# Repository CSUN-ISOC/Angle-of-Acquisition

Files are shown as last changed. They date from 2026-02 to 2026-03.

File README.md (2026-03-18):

# Angle-of-Acquisition
This is the repository for the AoA (Angle of Arrival) team's work throughout the semester. All files (source code and design files) relating to the AoA team and the Fibonacci Sphere can be found in this repository. Branches of this repository are meant for team members of the AoA team and their individual contributions to the project.

The primary goal of the AoA team this semester is to improve the design of the sphere and to give it the ability to adjust its positioning depending on the angle of an incoming modulated signal from a laser diode.

# Simulations


### Figure 1

Figure 1 shows the design of the 3D-printed servo mount in CAD. This servo will allow the sphere to rotate 360 degrees and tilt 15 degrees in each direction.



### Figure 2

Figure 2 shows a MATLAB simulation confirming proper operation of the entire Angle of Acquisition system. In this simulation, a theoretical flashlight is shined at the Fibonacci Sphere. The Fibonacci Sphere can identify where on the sphere the beam of light is shining by using data from all 64 of the photoresistors mounted on the sphere. From this, the sphere positions itself to make the beam of light shine on a receiver mounted to the exterior surface of the Fibonacci Sphere and thus allow the receiver to "focus" on the incoming data encoded into light source. The position of the flashlight changes every four seconds, and within those four seconds, the sphere is expected to move accordingly to line up the receiver to the beam of light. The square waves show the different positions of the light and the decaying graphs show the initial large error, which approaches zero in less than one second, meaning that the sphere properly identified the position of the incoming light and positioned the receiver as intended. This quick adjustment however, raised concerns about the forces that would result on the sphere, so the repositioning speed of the sphere was adjusted to be much slower. Even considering this adjustment, the sphere still has enough time to position itself and receive all of the incoming data.



### Figure 3

Figure 3 shows the design file for one quarter of the sphere. Due to its size, the Fibonacci Sphere had to be printed in quarters and attached together after the fact.

# Video Demonstrations
- Rotating the Fibonacci Sphere using Dummy Code:
  
  ISOC_Project

# Testing Documentation
The following media displays the testing that has gone into the designing, building, and programming of the Fibonacci Sphere and its respective circuitry.



### Figure 1

Figure 1 shows the initial attatchment of the servo mount that supports the sphere and is meant to allow the sphere to both rotate and tilt.



### Figure 2

Figure 2 shows how the servo mount is internally attached to the Fibonacci Sphere via nuts and bolts. Thread locker has been added to avoid loosening under vibration and/or shock.



### Figure 3

It was soon realized that the original shielded wiring that was used (black wires shown in Fig.2) were not necessary and were only more difficult to work with (i.e. to solder) due to them being frayed wires rather than solid. Figure 3 shows the old wires switched out for new red/blue wires with a solid core that allowed for easier soldering and a lighter load on the servo and its mount.



### Figure 4

Figure 4 gives a closer look at the wires inside the sphere to show that all wires have been labelled so that they can be connected to their proper terminals. Red wires all need to go to V<sub>CC</sub> and the blue wires will later be labeled to indicate which channel on which of the four multiplexers they belong to. This is to make diagnosis easier in the future.

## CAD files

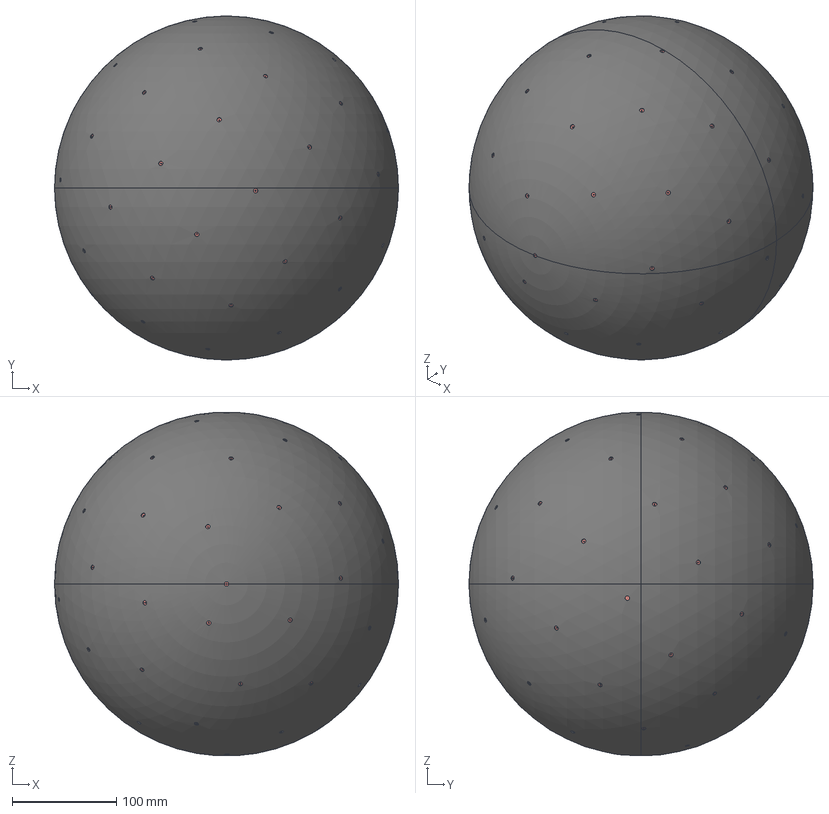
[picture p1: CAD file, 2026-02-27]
Sphere Design Files/Copy of Fibonacci Sphere v4 Whole.step
330.2 x 330.2 x 329.6 mm

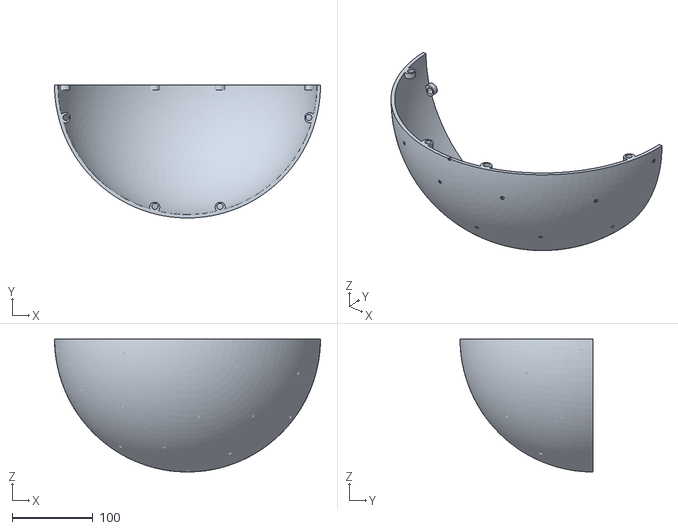
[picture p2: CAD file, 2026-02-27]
Sphere Design Files/Copy of Fibonacci Sphere v3 Bottom RIght.stl
330.2 x 165.1 x 165.0

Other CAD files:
Sphere Design Files/Copy of Fibonacci Sphere v4 Bottom Left.stl
Sphere Design Files/Copy of Fibonacci Sphere v4 Top Left.stl
Sphere Design Files/Copy of Fibonacci Sphere v4 Top RIght.stl
Sphere Design Files/Copy of Fibonacci Sphere v3 Whole.step

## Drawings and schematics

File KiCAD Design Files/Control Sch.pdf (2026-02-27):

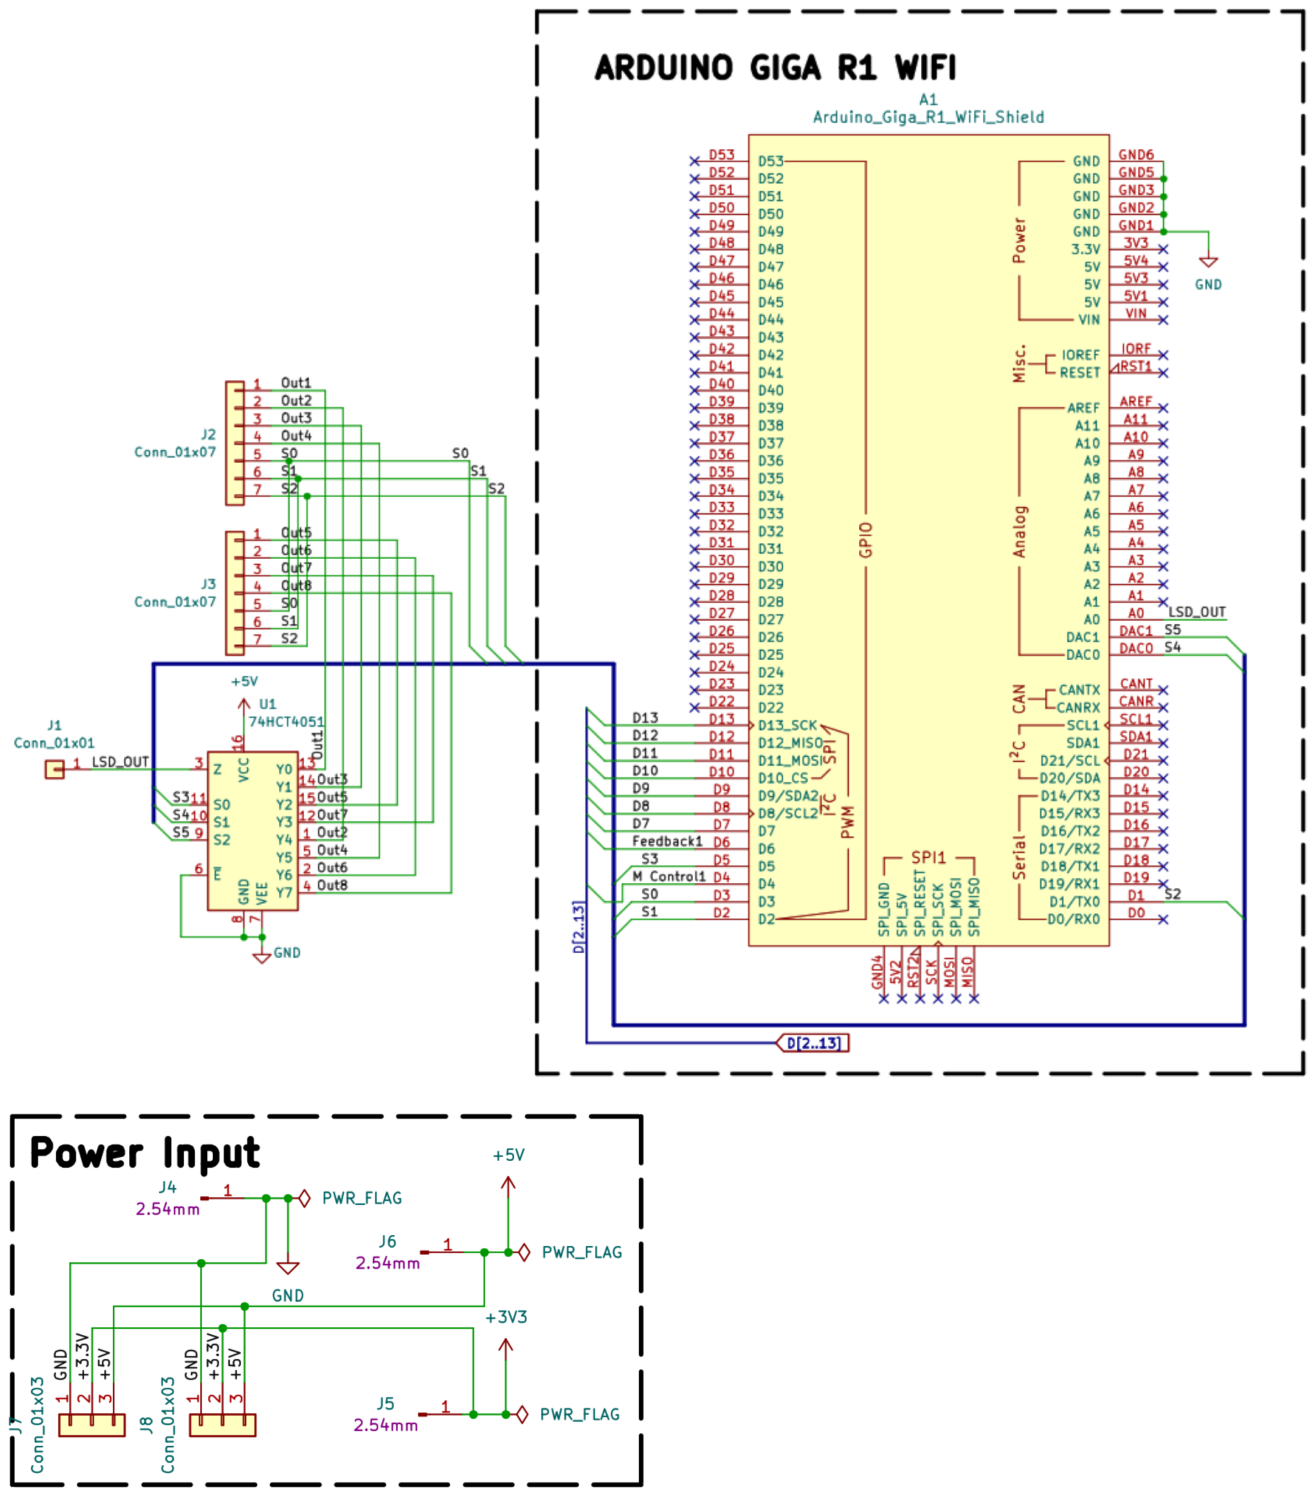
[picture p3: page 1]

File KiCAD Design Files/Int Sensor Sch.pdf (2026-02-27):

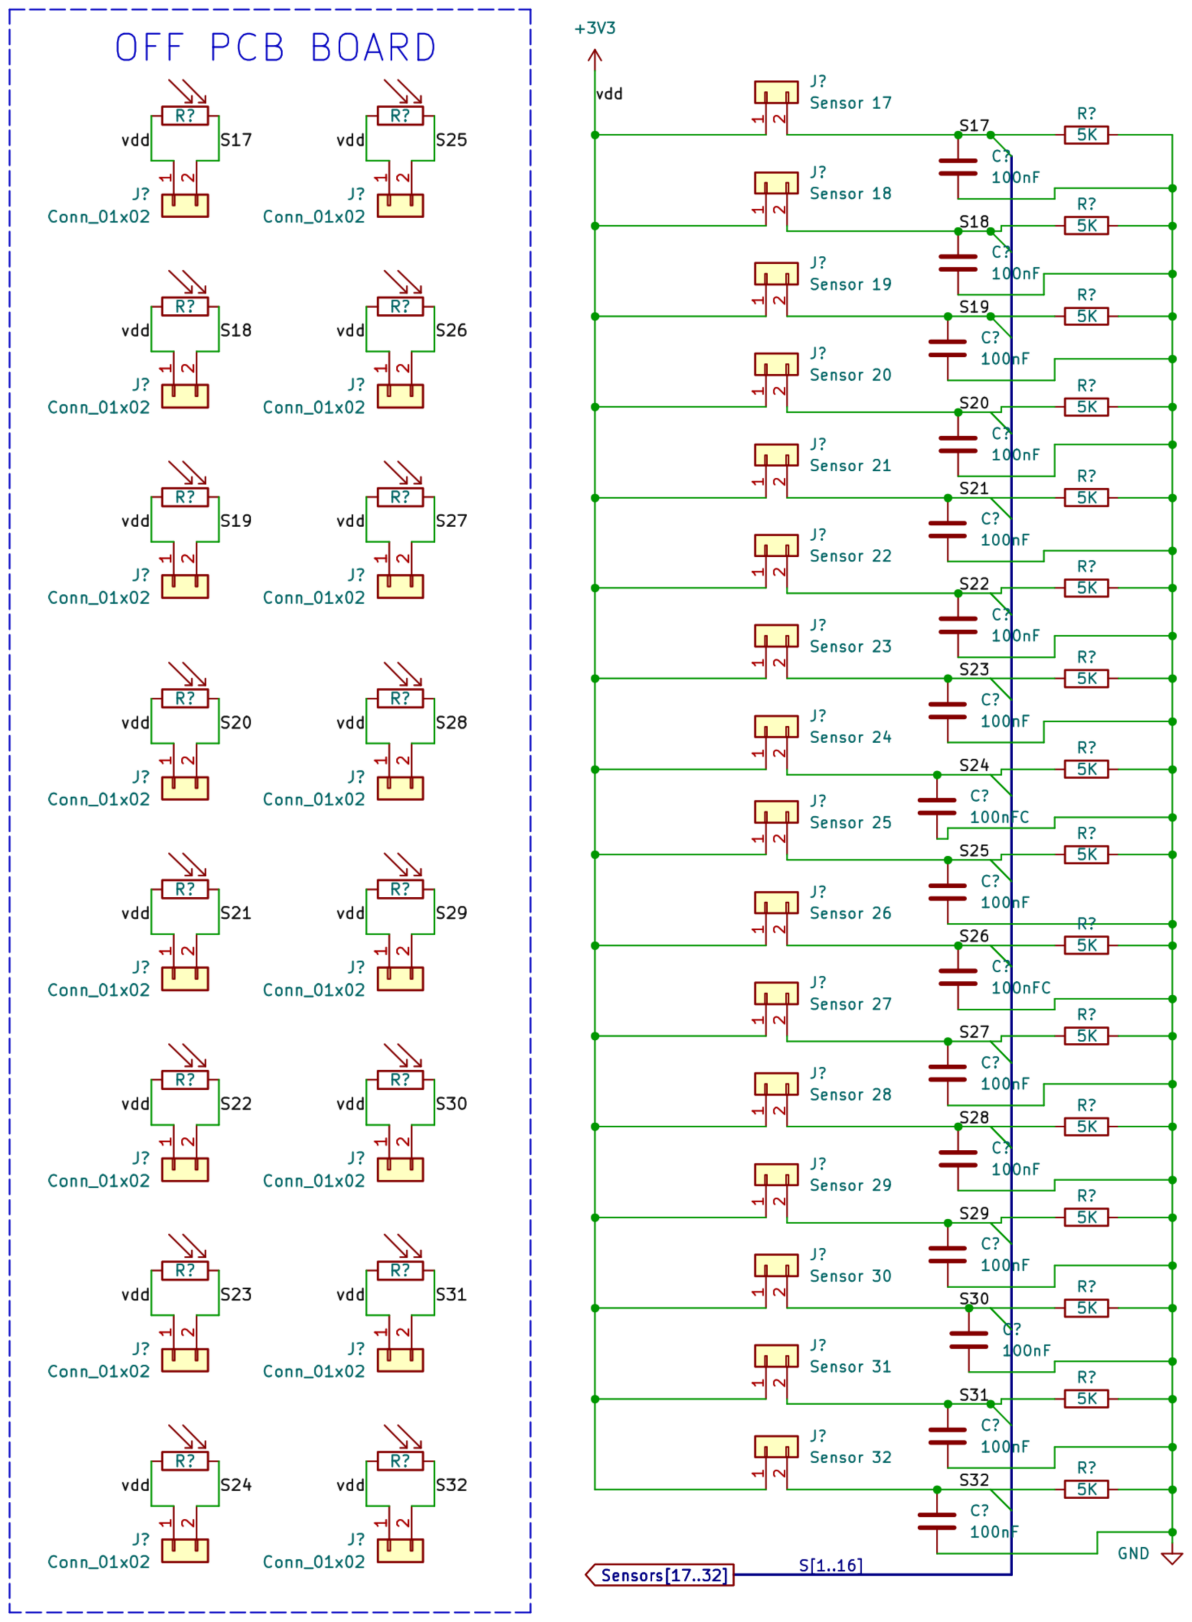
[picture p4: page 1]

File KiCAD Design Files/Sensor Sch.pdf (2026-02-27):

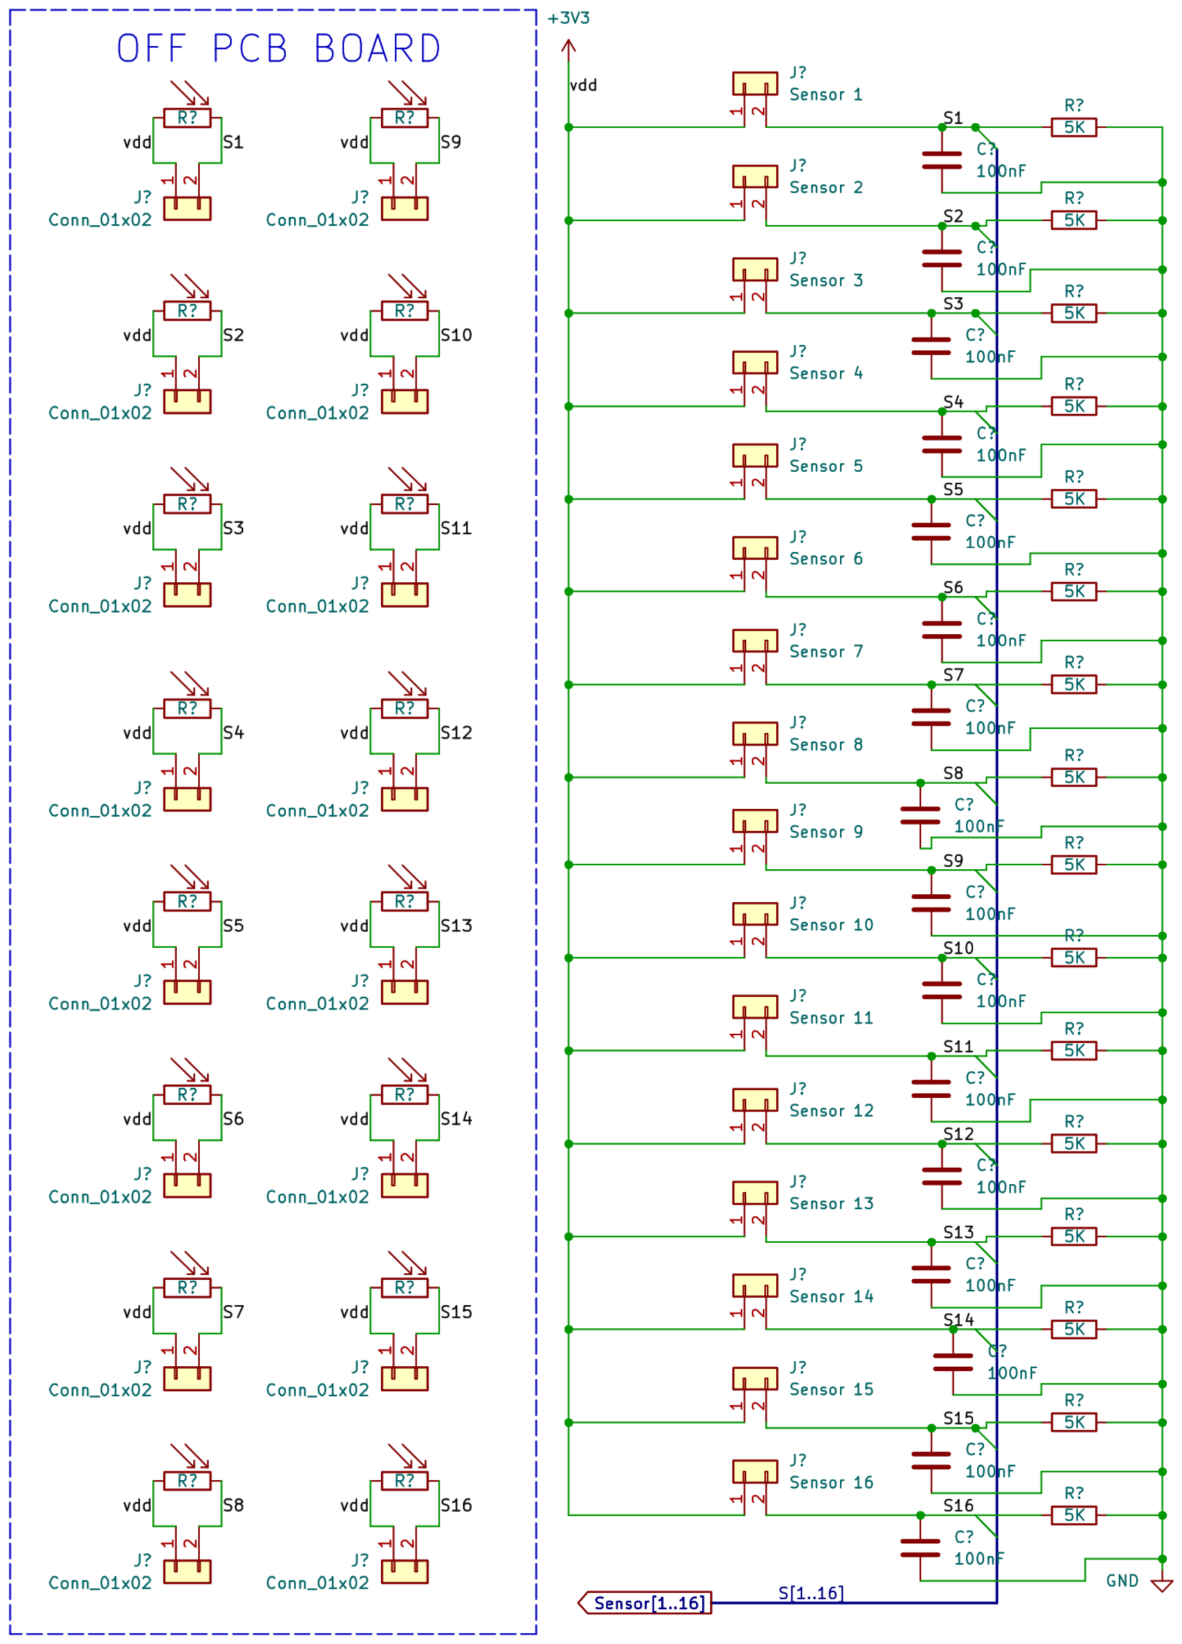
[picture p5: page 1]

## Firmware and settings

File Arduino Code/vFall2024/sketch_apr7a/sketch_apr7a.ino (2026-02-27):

#include "globals.h"
#include "matrix.h"
#include "muxControl.h"
#include "lightArray.h"
#include "FeedBackServo.h"
#include <RPC.h>

// Define pins
#define FEEDBACK_PIN 6   // Feedback pin connected to the feedback signal from the servo
#define SERVO_PIN 4      // Control pin for the servo

uint32_t activeSensor;
float* testIntensityReadings;

// set feedback signal pin number and constants
FeedBackServo feedbackServo(FEEDBACK_PIN);  // Create a FeedBackServo object

void setup() {
  /*
  // put your setup code here, to run once:
  //check to see which core is current
  pinMode(LEDB, OUTPUT); //blue led for M7
  pinMode(LEDG, OUTPUT); //green led for M4
   if(RPC.cpu_id() == CM7_CPUID){
    blink(LEDB, 100); //blink  blue led (M7 Core)
   } else {
    blink(LEDG, 100); //blink green led(M4 core)
   }
  RPC.begin(); //initialize 2nd core
  //end of core check
  */

  pinMode(LED_BUILTIN, OUTPUT);
	activeSensor= 0; //currently selected sensor
	testIntensityReadings = nullptr; //initialize test intensity readings
	lightArrayInit(activeSensor); //initialize mux controls
  Serial.begin(9600);
  analogReadResolution(12);
  pinMode(D5, OUTPUT);
  pinMode(D3, OUTPUT);
  pinMode(D2, OUTPUT);
  pinMode(D1, OUTPUT);
  lightArrayBaseline(); //take baseline
  
  digitalWrite(LED_BUILTIN, LOW);   // turn the LED off by making the voltage LOW
  digitalWrite(LED_BUILTIN, HIGH);  // turn the LED on (HIGH is the voltage level)
  delay(100);                      // wait for a second
  digitalWrite(LED_BUILTIN, LOW);   // turn the LED off by making the voltage LOW
  delay(100);                      // wait for a second
  digitalWrite(LED_BUILTIN, HIGH);  // turn the LED on (HIGH is the voltage level)
  delay(100);                      // wait for a second
  digitalWrite(LED_BUILTIN, LOW);   // turn the LED off by making the voltage LOW
  delay(100);                      // wait for a second
  digitalWrite(LED_BUILTIN, HIGH);  // turn the LED on (HIGH is the voltage level)
  delay(100);                      // wait for a second
  digitalWrite(LED_BUILTIN, LOW);   // turn the LED off by making the voltage LOW
  delay(100);                      // wait for a second
  digitalWrite(LED_BUILTIN, HIGH);  // turn the LED on (HIGH is the voltage level)
  delay(100);                      // wait for a second
  digitalWrite(LED_BUILTIN, LOW);   // turn the LED off by making the voltage LOW
  

  //servo part, sets motor pin
  feedbackServo.setServoControl(SERVO_PIN);  // Attach the servo control to the pin
  feedbackServo.setKp(1.0);  // Optional: Set a custom proportional gain for rotation
}

void loop() {
  lightArraySampleSensors();

  for (int i = 0; i < g_sensorCount; i++) {
    Serial.print("Sensor[");
    Serial.print(i);
    Serial.print("]: ");
    Serial.print(100 * g_sensorIntensityVector.element[i][0], 5);
    Serial.print("% - ");
    Serial.println(g_muxADCReadings[i]);
  }

  auto [azimuth, elevation] = lightArrayCalculateAoA3D();

  Serial.print("Azimuth: ");
  Serial.print(azimuth, 2);
  Serial.print("°, Elevation: ");
  Serial.print(elevation, 2);
  Serial.println("°");
  delay(500);

  // Rotate to Azimuth
  Serial.print("Rotating to AoA Azimuth: ");
  Serial.println(static_cast<int>(azimuth));
  feedbackServo.rotate(static_cast<int>(azimuth), 4);

  delay(1000);  // Wait 1s between readings
}

  /*
  //leds that turn on trying to show that it is being setup
  digitalWrite(LED_BUILTIN, HIGH);  // turn the LED on (HIGH is the voltage level)
  delay(200);                      // wait for a second
  digitalWrite(LED_BUILTIN, LOW);   // turn the LED off by making the voltage LOW
  delay(200);                      // wait for a second
  digitalWrite(LED_BUILTIN, HIGH);  // turn the LED on (HIGH is the voltage level)
  delay(200);                      // wait for a second
  digitalWrite(LED_BUILTIN, LOW);   // turn the LED off by making the voltage LOW
  */

  // Serial.println("Sensor[1]: ");
  // Serial.println(testIntensityReadings[1],32);
  // Serial.println("Sensor[2]: ");
  // Serial.println(testIntensityReadings[2],32);
  // Serial.println("Sensor[3]: ");
  // Serial.println(testIntensityReadings[3],32);
  // Serial.println("Sensor[4]: ");
  // Serial.println(testIntensityReadings[4],32);
  // Serial.println("Sensor[5]: ");
  // Serial.println(testIntensityReadings[5],32);
  // Serial.println("Sensor[6]: ");
  // Serial.println(testIntensityReadings[6],32);
  // Serial.println("Sensor[7]: ");
  // Serial.println(testIntensityReadings[7],32);
  // Serial.println("Sensor[8]: ");
  // Serial.println(testIntensityReadings[8],32);
  // Serial.println("Sensor[9]: ");
  // Serial.println(testIntensityReadings[9],32);
  // Serial.println("Sensor[10]: ");
  // Serial.println(testIntensityReadings[10],32);
  // Serial.println("Sensor[11]: ");
  // Serial.println(testIntensityReadings[11],32);
  // Serial.println("Sensor[12]: ");
  // Serial.println(testIntensityReadings[12],32);
  // Serial.println("Sensor[13]: ");
  // Serial.println(testIntensityReadings[13],32);
  // Serial.println("Sensor[14]: ");
  // Serial.println(testIntensityReadings[14],32);
  // Serial.println("Sensor[15]: ");
  // Serial.println(testIntensityReadings[15],32);
  



/*
//code core check
void blink(int led, int delaySeconds) {
    for(int i; i < 3; i++) {
      digitalWrite(led, LOW);
      delay(delaySeconds);
      digitalWrite(led, HIGH);
      delay(delaySeconds);
    }
  
  }
  //end of 2nd core blink
*/

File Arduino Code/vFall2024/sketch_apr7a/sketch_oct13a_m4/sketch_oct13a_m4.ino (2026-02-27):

#include <RPC.h>

void setup() {
  // put your setup code here, to run once:
  pinMode(LEDB, OUTPUT);
  pinMode(LEDG, OUTPUT);

  if(RPC.cpud_id() == CM7_CPUID) {
    blink(LEDB, 100);
  } else {
    blink(LEDG, 100);
  }
  RPC.begin();
}

void loop() {
  // put your main code here, to run repeatedly:
  
}

void blink(int led, int delaySeconds) {
    for (int i; i<5; i++) {
      digitalWrite(led, LOW);
      delay(delaySeconds);
      digitalWrite(led, HIGH);
      delay(delaySeconds);
    }
  }

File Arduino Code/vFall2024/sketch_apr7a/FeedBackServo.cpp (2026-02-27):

#include <Arduino.h>
#include <Servo.h>
#include "FeedBackServo.h"

Servo FeedBackServo::Parallax;
byte FeedBackServo::feedbackPinNumber = 2;
volatile int FeedBackServo::angle;
float FeedBackServo::thetaPre;
unsigned int FeedBackServo::tHigh, FeedBackServo::tLow;
unsigned long FeedBackServo::rise, FeedBackServo::fall;
int FeedBackServo::turns = 0;
float FeedBackServo::Kp = 1.0;
const int FeedBackServo::unitsFC = 360;
const float FeedBackServo::dcMin = 0.029;
const float FeedBackServo::dcMax = 0.971;
const int FeedBackServo::dutyScale = 1;
const int FeedBackServo::q2min = unitsFC / 4;
const int FeedBackServo::q3max = q2min * 3;

FeedBackServo::FeedBackServo(byte _feedbackPinNumber)
{
    pinCheck(_feedbackPinNumber);
    feedbackPinNumber = _feedbackPinNumber;
    byte internalPinNumber = digitalPinToInterrupt(feedbackPinNumber);
    attachInterrupt(internalPinNumber, feedback, CHANGE);
}

void FeedBackServo::setServoControl(byte servoPinNumber)
{
    Parallax.attach(servoPinNumber);
}

void FeedBackServo::setKp(float _Kp)
{
    Kp = _Kp;
}

void FeedBackServo::rotate(int degree, int threshold)
{
    float output, offset, value;
    unsigned long startMillis = millis();  // Track when the rotation started
    unsigned long timeout = 1000; // Timeout after 1 seconds to avoid infinite loop

    // Continuously adjust the servo position until it is within the threshold range
    while (abs(degree - angle) > threshold) {
        output = (degree - angle) * Kp;  // Calculate error and output
        if (output > 200.0) output = 200.0;  // Cap output
        if (output < -200.0) output = -200.0;
        
        offset = (degree > angle) ? 30.0 : (degree < angle) ? -30.0 : 0.0; // Adjust for small corrections
        value = output + offset;  // Final value to set

        Parallax.writeMicroseconds(1490 - value);  // Move the servo

        // If the servo hasn't reached its target after 1 seconds, stop the rotation
        if (millis() - startMillis > timeout) {
            Serial.println("Rotation timeout reached.");
            break;
        }

        delay(15);  // Small delay to allow the servo to move
    }

    // After the rotation is complete, stop the servo at the target position
    Parallax.writeMicroseconds(1490);  // Stop the servo at the target position
}

int FeedBackServo::Angle()
{
    return angle;
}

void FeedBackServo::pinCheck(byte _feedbackPinNumber)
{
#ifdef ARDUINO_AVR_UNO
    if (_feedbackPinNumber != 2 && _feedbackPinNumber != 3)
        exit(1);
#endif
#ifdef ARDUINO_AVR_LEONARDO
    if (_feedbackPinNumber != 0 && _feedbackPinNumber != 1 && _feedbackPinNumber != 2 && _feedbackPinNumber != 3 && _feedbackPinNumber != 7)
        exit(1);
#endif
}

void FeedBackServo::feedback()
{
    if (digitalRead(feedbackPinNumber))
    {
        rise = micros();
        tLow = rise - fall;

        int tCycle = tHigh + tLow;
        if ((tCycle < 1000) || (tCycle > 1200))
            return;

        float dc = (dutyScale * tHigh) / (float)tCycle;
        float theta = ((dc - dcMin) * unitsFC) / (dcMax - dcMin);

        if (theta < 0.0)
            theta = 0.0;
        else if (theta > (unitsFC - 1.0))
            theta = unitsFC - 1.0;

        if ((theta < q2min) && (thetaPre > q3max))
            turns++;
        else if ((thetaPre < q2min) && (theta > q3max))
            turns--;

        if (turns >= 0)
            angle = (turns * unitsFC) + theta;
        else if (turns < 0)
            angle = ((turns + 1) * unitsFC) - (unitsFC - theta);

        thetaPre = theta;
    }
    else
    {
        fall = micros();
        tHigh = fall - rise;
    }
}

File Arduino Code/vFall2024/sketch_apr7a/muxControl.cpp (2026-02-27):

#include "muxControl.h"

muxControlPinMap muxControlInit(uint32_t** decimalBinaryMapping, uint32_t& activeSensor, const uint32_t* muxPinList, const uint32_t controlPinCount, const uint32_t sensorCount)
{
	muxControlPinMap activeControlPins; //create control pin map
	activeControlPins.muxPin = nullptr;
	activeControlPins.muxPinDec = nullptr;
	activeControlPins.muxPinCount = 0;
	activeControlPins.muxPins = 0;
	muxControlAddControlPins(activeControlPins, muxPinList, controlPinCount); //load up mux control pin mappings with decimal mapping to one-hot
	*decimalBinaryMapping = muxControlBinaryMapping(activeControlPins, sensorCount); //this maps the sensors to the muxes control lines of the pin mappings
	activeSensor = (uint32_t)0; //initialize control pin signals
	muxControlWriteControlPins(activeControlPins, *decimalBinaryMapping[activeSensor]); //initial control pin signals asserted
	return activeControlPins;
}


void muxControlAddControlPins(muxControlPinMap &controlPinMap, const uint32_t* bits, const uint32_t arr_length)
{

	if (controlPinMap.muxPin != nullptr || controlPinMap.muxPinDec != nullptr) //if had mux pins assigned before, delete them
	{
		if (controlPinMap.muxPin != nullptr)
		{
			delete[] controlPinMap.muxPin;
			controlPinMap.muxPin = nullptr;
		}
		if (controlPinMap.muxPinDec != nullptr)
		{
			delete[] controlPinMap.muxPinDec;
			controlPinMap.muxPinDec = nullptr;
		}
	}
	controlPinMap.muxPinCount = arr_length;
	controlPinMap.muxPins = (uint32_t)0;
	controlPinMap.muxPin = new uint32_t[controlPinMap.muxPinCount];
	controlPinMap.muxPinDec = new uint8_t[controlPinMap.muxPinCount];

	uint32_t i = 0;
	for (i = 0; i < controlPinMap.muxPinCount; i++)
	{
		controlPinMap.muxPinDec[i] = bits[i]; //store the decimal value that indicates the pin
		controlPinMap.muxPin[i] = ((uint32_t)1) << controlPinMap.muxPinDec[i];//shift over 1 into the bit position, then add the result to the of muxs control pins list
		controlPinMap.muxPins |= controlPinMap.muxPin[i]; //add mux control pin to all mux control pins 
	}

	return;
}

uint16_t muxControlReadPin(void)
{
	return analogRead(A11); //GIGA's analog resolutions are 16 bit
}

//selects the next sensor
//not used. Could be used if generalized. make g_sensorCount a parameter
void inline muxControlNextSensor(muxControlPinMap& controlPinMap, uint32_t& muxControlValue)
{
	if (muxControlValue >= g_sensorCount - 1)
		muxControlValue = 0;
	else
		muxControlValue++;
	muxControlWriteControlPins(controlPinMap, muxControlValue);
}

void muxControlWriteControlPins(const muxControlPinMap controlPinMap, const uint32_t muxSelectedControlLines)
{
	//input validation is not done, to decrease delay
	//if (controlPinMap.muxPin == nullptr || controlPinMap.muxPinDec == nullptr || controlPinMap.muxPinCount == 0)
		//return;
	GPIOA->ODR &= ~controlPinMap.muxPins;//clear all control bits
	GPIOA->ODR |= muxSelectedControlLines; //assert/deassert the control bits
}

//maps a decimal value to the binary control bits, LSB to MSB
uint32_t muxControlMapToBinary(const muxControlPinMap controlPinMap, const uint32_t value)
{
	//value is in binary, now we need to shift all the bits to the right place

	if (controlPinMap.muxPin == nullptr || controlPinMap.muxPinDec == nullptr || controlPinMap.muxPinCount == 0)
		return 0xFFFFFFFF; //all ones for error
	uint32_t bit; //current bit value at index i
	uint32_t controlBits = 0; //current control bits
	for (int i = 0; i < controlPinMap.muxPinCount; i++)
	{
		bit = value >> i;//controlPinMap.muxPinDec[i]; //shift by the position of the ith control bit
		bit <<= controlPinMap.muxPinDec[i];
		bit &= controlPinMap.muxPin[i]; //isolates the shifted bit
		controlBits |= bit; //adds the shifted bit to the control bits
	}
	return controlBits;
}

//maps all decimal values to the binary control bits, LSB to MSB
uint32_t* muxControlBinaryMapping(const muxControlPinMap controlPinMap, const uint32_t sensorCount)
{
	//value is in binary, now we need to shift all the bits to the right place

	if (controlPinMap.muxPin == nullptr || controlPinMap.muxPinDec == nullptr || controlPinMap.muxPinCount == 0)
		return nullptr;
	uint32_t* mappings = new uint32_t[sensorCount];
	uint32_t i = 0;
	for (i = 0; i < sensorCount; i++)
	{
		mappings[i] = muxControlMapToBinary(controlPinMap, i);
		if (mappings[i] == 0xFFFFFFFF)
		{
			delete[] mappings;
			return nullptr;
		}
	}
	return mappings;
}

void muxControlReadPins(const muxControlPinMap controlPinMap, const uint32_t* decimalBinaryMapping, uint16_t* &ADC_reading, uint32_t &activeSensor, const uint32_t sensorCount)
{
	if (ADC_reading == nullptr)
		ADC_reading = new uint16_t[sensorCount];
	uint32_t i = 0;
	//float temp[] = { 0.866025403784439, 0.991444861373811, 0.965925826289068 ,0.793353340291235, 0.500000000000000,0.130526192220052,0,0,0,0,0,0,0,0,0.258819045102521,0.608761429008721 };

	for (i = 0; i < sensorCount; i++)
	{
		/*
		When VEE is grounded:
		Max propagation delay of two HCT Muxes in series: 24 ns
		Max frequency of two HCT Muxes in series: 41.67 MHz

		When VEE is a negative volt source:
		Max propagation delay of two HCT Muxes in series: 16 ns
		Max frequency of two HCT Muxes in series: 62.50 MHz 
		*/

		muxControlWriteControlPins(controlPinMap, decimalBinaryMapping[i]); //assert new control line values
		//for (int j = 0; j < 2; j++) //we require 24 ns to account for max propagation, there is about 6 cycles per loop = 12.5 ns, so require 2 loops for total of 25 ns
		delayMicroseconds(40000);
    //asm volatile("nop"); asm volatile("nop"); asm volatile("nop"); asm volatile("nop"); asm volatile("nop"); asm volatile("nop"); //delays for one clock cycle, aka 2.083ns if 480 MHz [asm volatile("nop")] <--In arduino sketches
		//asm volatile("nop"); asm volatile("nop"); asm volatile("nop"); asm volatile("nop"); asm volatile("nop"); asm volatile("nop");
		ADC_reading[i] = muxControlReadPin();//(uint16_t)(temp[i] * 65535);//muxControlReadPin();//(uint16_t)(temp[i] * 65535);//muxControlReadPin(); //read adc reading
	}
	activeSensor = i - 1;

	return;
}
